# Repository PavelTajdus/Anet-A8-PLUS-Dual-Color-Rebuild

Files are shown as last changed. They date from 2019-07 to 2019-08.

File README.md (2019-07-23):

# Anet A8 PLUS Dual Color Rebuild

Kamarád chtěl postavit dual color tiskárnu. Jako základ pro dvoubarevný tisk jsem zvolil Anet A8Plus, která vypadala jako solidní základ pro předělávku. Později se ukázalo, že to nebyla nejšťastnější volba, ale tiskárna už byla doma, takže jsem si s tím musel poradit.

Protože tiskárna z výroby není moc dobře udělaná (profily nemají stejné délky - lítá to až o milimetr), závitovky nejsou rovné atd atd, musel jsem trochu přepracovat některé díly. Nakonec jsem toho přepracovával hodně :-)

Z původní tiskárny jsem použil profily, tyče, závitovky, motory, endstopy a pár kabelů. Zbytek jsem předělal.

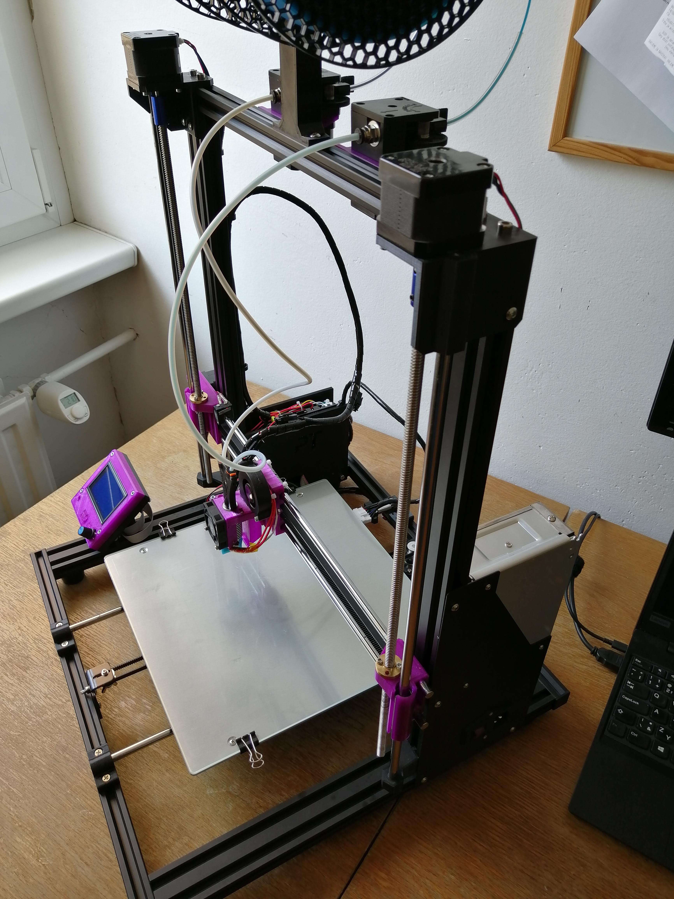
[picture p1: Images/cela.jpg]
PT Anet A8Plus Dual Color


## Dual Color

Jako systém pro dvoubarevný tisk jsem zvolil systém dvou extruderů do jednoho hotendu (Y joiner). Jedná se o relativně jednoduché řešení, které podporuje i mnou používaný Prusa Slicer 2.0.

Použil jsem klona V6 hotendu s bore 4.1 heatbreakem. Používá se proto, aby do hotendu šla tenčí PTFE o průměru 1,9mm, a do "joineru" pak klasická PTFE o průměru 2,0mm. Zabezpečí se tím hladší chod filamentu v "joineru".

## Vyměněné díly

Kvůli použití dvou extruderů jsem musel měnit i desku. Zvolil jsem SKR v1.3, což je 32bitová deska za výbornou cenu. Dokonce levnější než originální Anet deska. Origo deska má integrované drivery, takže jsem k SKR nakoupil 5x TMC2208, které jsem zapojil v UART. Díky tomu se dají drivery ovládat z Firmware a nastavovat jejich mod, hybrid treshold a jiné srandy.

Abych zajistil dostatečně kvalitní podávání filamentu, rozhodl jsem se pro Titan extruder (opět klony). Mám s nimi dobré zkušenosti - dobře se zavádí a vyndavá filament (oproti BMG). A je za super cenu.

Protože jsem nebyl absolutně schopný vyrovnat podložku standardními levlovacími šrouby, rozhodl jsem se pro 3Dtouch. Měl jsem dva různé senzory, jeden od Trianglelab, druhý od Fysetc. Fysetc skončil v koši. Absolutně k ničemu. Trianglelab naštěsti funguje obstojně. Podložku jsem přišrouboval napevno pomocí distančních sloupků.

Další výměna mě čekala u displeje. Nebyl jsem schopný rozhýbat originální přibalený displej, tak jsem použil klasický velký 12864 LCD displej se čtečkou karet. Čtečka karet v displeji je mnohem příjemnější pro obsluhu než lovit malou mikro sd kartu za tiskárnou v desce.

Měnil jsem i část kabeláže, protože například kabel od zdroje mi nedosáhl k desce, aniž by visel pod bedem. Kabeláž k hotendu jsem doplnil o konektory, aby se hotend dal kompletně sundat bez nutnosti odpojování kabeláže z desky. Veškerou kabeláž jsem pak omotal omotávkou dodávanou k tiskárně a kabely přichytil do profilů spojkami.

### Motory vzhůru!

Umístit motory nahoře bylo řešením několika problémů. Závitové tyče nebyly naprosto rovné. Jedna ano, druhá ne. Při otáčení závitovkou tyč ovlivňovala osu X, což ovlivní kvalitu tisku. Další problém byl, že došlo ke snížení bedu o nějaký ten centimetr a díky změně hotendu a extruderu už nebylo možné dostat se tryskou na tiskovou podložku. Umístěním motorů nahoru všechny tyhle neduhy vyřešilo. A nepřišlo se ani o milimetr z tiskové výšky stroje. Naopak by se dalo ještě pár cm přidat, ale na úkor snížení pevnosti držáků motoru. Což mi přišlo zbytečné.

## Seznam dokoupených dílů

### Elektronika
- [Deska SKR V1.3](https://www.aliexpress.com/item/32980090169.html)
- [5x TMC 2208](https://www.aliexpress.com/item/32980090169)
- [Motor extruderu](https://www.aliexpress.com/item/32377416566.html)
- [Dlouhé kabely k motorům](https://www.aliexpress.com/item/33015610522.html)
- [Rozdvojka konektorů pro Z motory](https://www.aliexpress.com/item/32849801852.html)
- [Trianglelab 3D Touch](https://www.aliexpress.com/item/32832887426.html)
- [12864 LCD displej se čtečkou karet](https://www.aliexpress.com/item/32516184695.html)
- [Stepdowny na 12V](https://www.aliexpress.com/item/32725444495.html)
- [5015 ventilátor Sunon 12V - ofuk výtisku](https://www.official.cz/z5376-ventilator-sunon-gb1205phvx-8ay-gn)
- [4010 ventilátor Sunon 12V - hotend](https://www.gme.cz/ventilator-sunon-ee40101s2-1000u-999)
- [6015 ventilátor Sunon 12V - do zdroje](https://www.gme.cz/ventilator-sunon-kd1206phs3)
- [50x50 tichý ventilátor Sillentium PC 12V - ofuk desky](https://www.czc.cz/silentiumpc-zephyr-50-50mm/134487/produkt)
- [Přívodní kabely průměr 4mm ze zdroje k desce](https://www.emat.cz/index.php?route=product/search&search=H07V-K%204)
- [Konektory pro připojení endstopů a další kabeláže do desky (XH2.54 2 Pin)](https://www.aliexpress.com/item/32821493939.html)
- [Konektory pro spojení kabeláže hotendu](https://www.aliexpress.com/item/32843315324.html)

### Hardware
- [Titan Extruder](https://www.aliexpress.com/item/32789942768.html)
- [V6 hotend 4.1 bore](https://www.aliexpress.com/item/32911028903.html)
- [Silikonový návlek na hotend](https://www.aliexpress.com/item/32920518452.html)
- [Trianglelab TL-Feeder ("joiner" - Y spojka)](https://www.aliexpress.com/item/32770576556.html)
- [PTFE (ačkoliv jsou dodané k joineru, dával jsem jiné)](https://www.aliexpress.com/item/32814232529.html)
- [Distanční sloupky k bedu](https://www.gme.cz/distancni-trubicka-mdr4305)
- [Pevné spojky závitové tyče a motoru 5x8mm](https://www.aliexpress.com/item/32957956109.html)
- [Ložisko LM8UU (vozík osy x)](https://www.aliexpress.com/item/32317938156.html)
- [Šrouby M4 různých délek](https://eshop.killich.cz/eshop/nerezovy-spojovaci-material/srouby-zatky/imbusy-vnitrni-sestihran/din-912-imbus-s-valcovou-hlavou/)
- [Stahovací pásky](https://www.aliexpress.com/item/32868074097.html)
- [Matky do profilů M4](https://www.aliexpress.com/item/32799858611.html)

### Tištěné díly

Viz seznam dílů [ve složce STL](https://github.com/PavelTajdus/Anet-A8-PLUS-Dual-Color-Rebuild/tree/master/STL).

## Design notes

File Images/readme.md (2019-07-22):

PT Anet A8Plus Dual Color
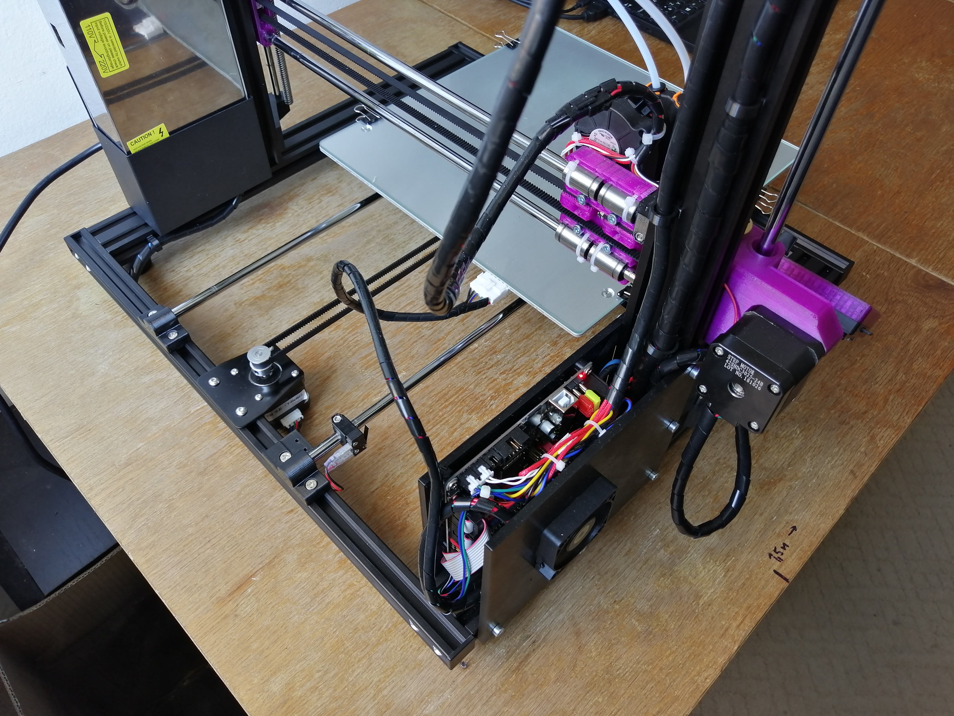
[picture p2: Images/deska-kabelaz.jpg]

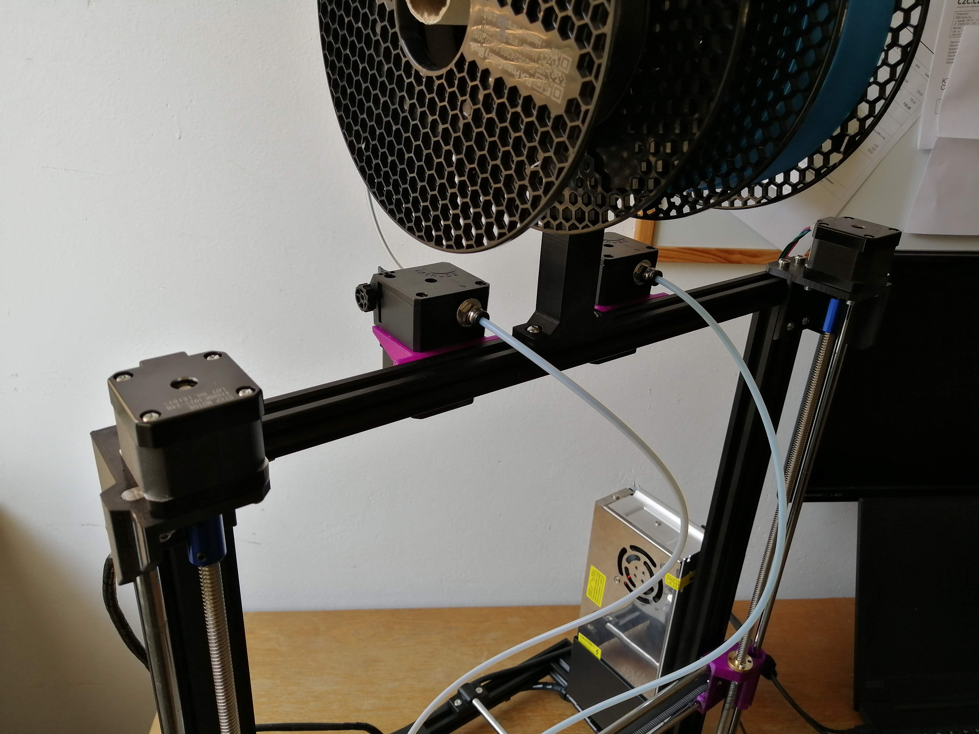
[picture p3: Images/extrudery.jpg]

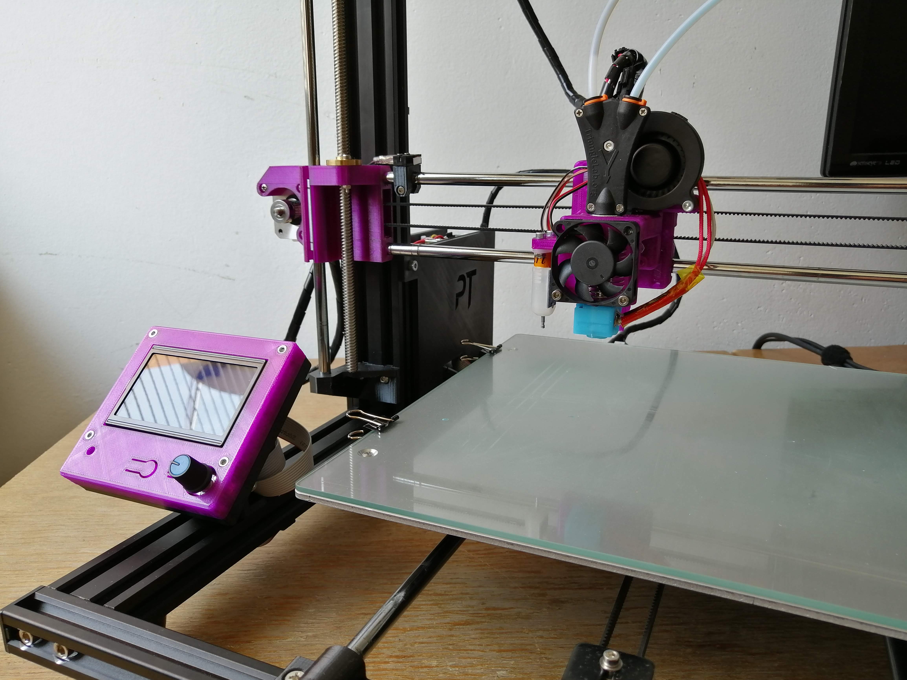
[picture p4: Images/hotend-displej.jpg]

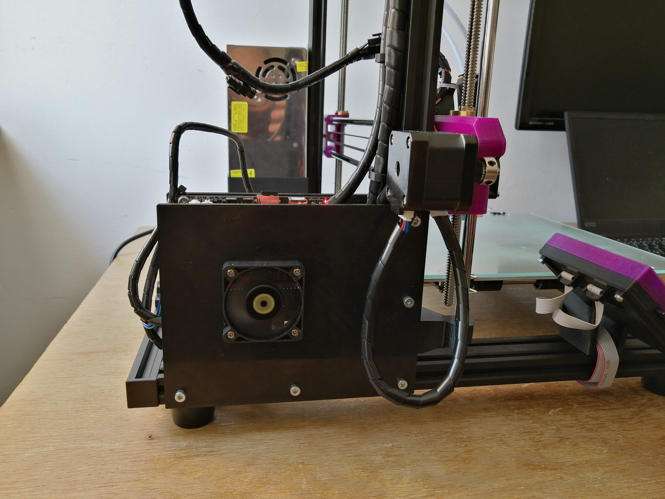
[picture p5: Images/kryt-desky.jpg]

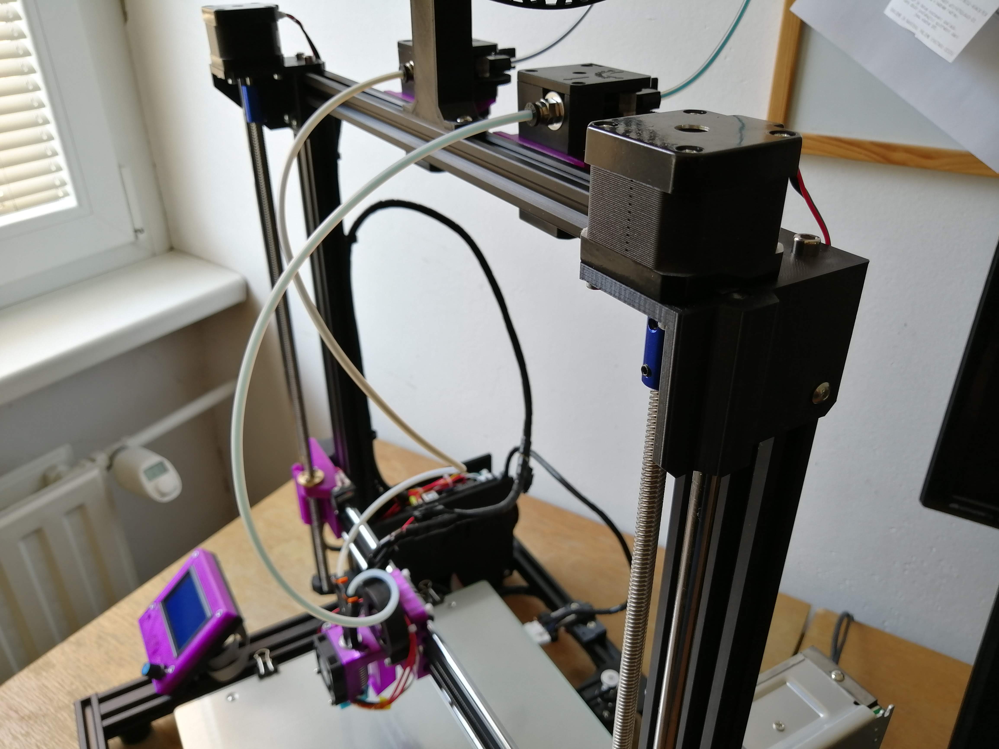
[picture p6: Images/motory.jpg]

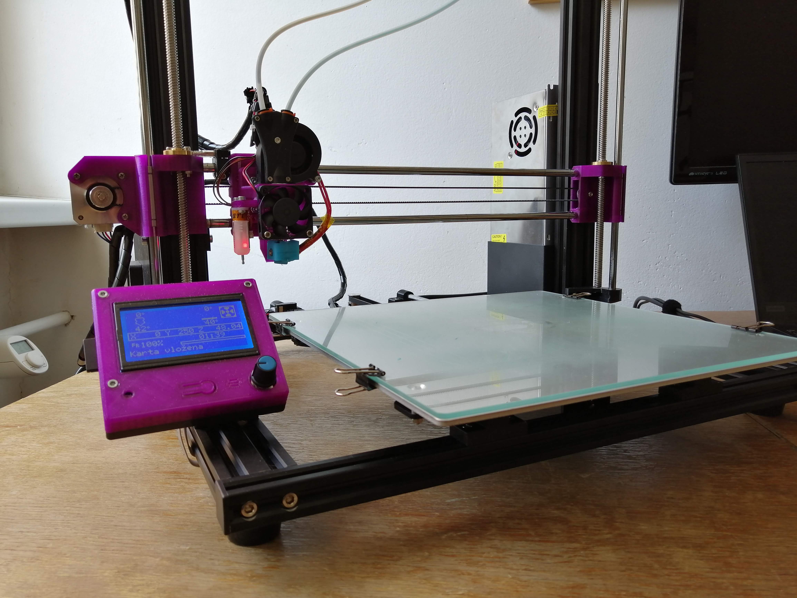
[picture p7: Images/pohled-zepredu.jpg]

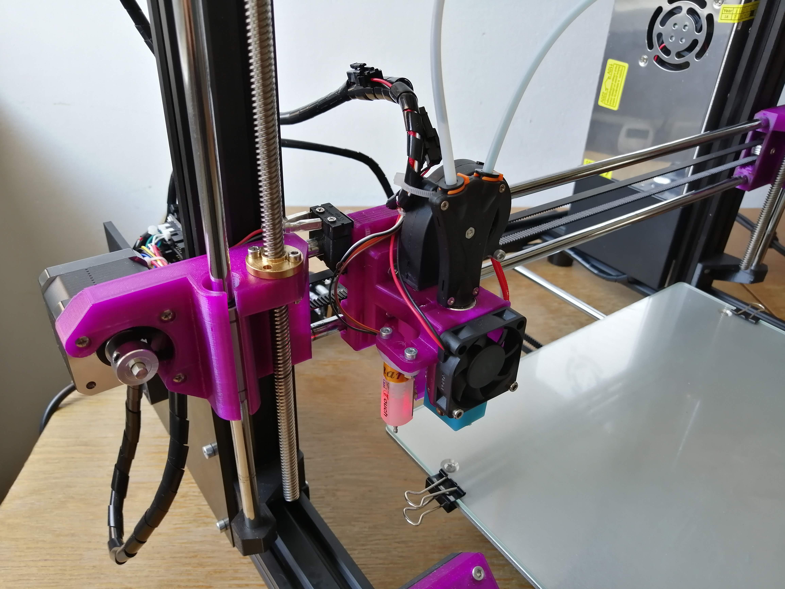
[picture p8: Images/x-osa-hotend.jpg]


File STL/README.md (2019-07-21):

# STL soubory pro přestavbu tiskárny

Většinu dílů jsem si navrhl, protože jsem nebyl schopný najít odpovídající řešení na thingiverse nebo jinde. Díly které jsem nenavrhoval zde uvádím v odkaze na thingiverse. Ale zároveň je najdete zde jako STL.

Kompletně jsem předělal osu X. Anet používá jiné rozměry než i3 standard, což mě omezovalo v použítí různých pojezdů a držáků hotendu. Proto jsem předělal osu X aby používala rozteč tyčí 45 mm.

Kvůli zvolenému systému pro Dual Color jsem vybral V6 hotend s bore 4.1 heatbreakem. A použil oblíbený držák z Hypercube. Používám 40mm větráky, a 3Dtouch. Veškeré díly jsou jak v STL souborech, tak v odkazech.

## Odkazy na použité komponenty:
- [Kryt na displej - Discount Full Graphic Smart Controller](https://www.thingiverse.com/thing:2368534)
- [Držák V6 hotendu](https://www.thingiverse.com/thing:1632847)
- [Redukce na 40mm ventilátor pro držák hotendu](https://www.thingiverse.com/thing:2716350)
- [X vozík pro hotend](https://www.thingiverse.com/thing:586636)

### Doporučené příslušenství

- [Klipy na kabely](https://www.thingiverse.com/thing:3102684)
- [Klipy na kabely k displeji](https://www.thingiverse.com/thing:2626246)

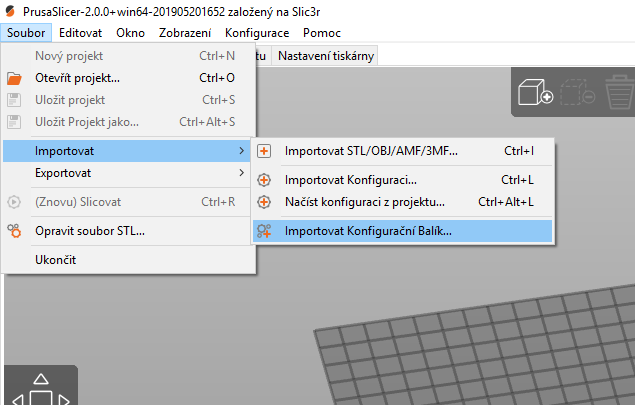
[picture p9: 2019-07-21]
Images/import-balicku.png

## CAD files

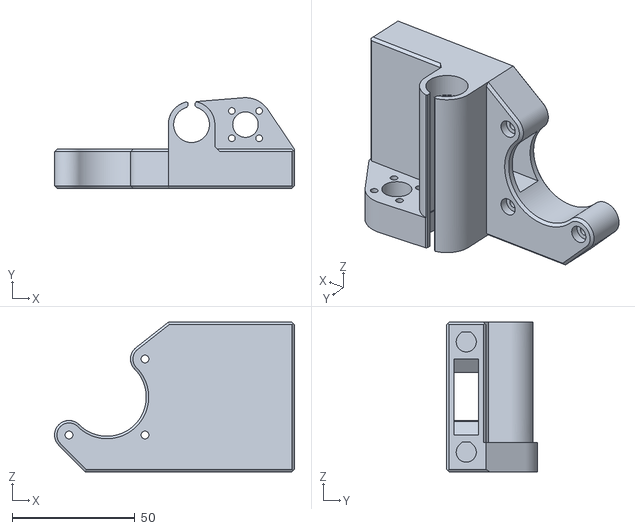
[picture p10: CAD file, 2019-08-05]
STL/x-osa-motor-idler.stl
97.9 x 37.0 x 61.0

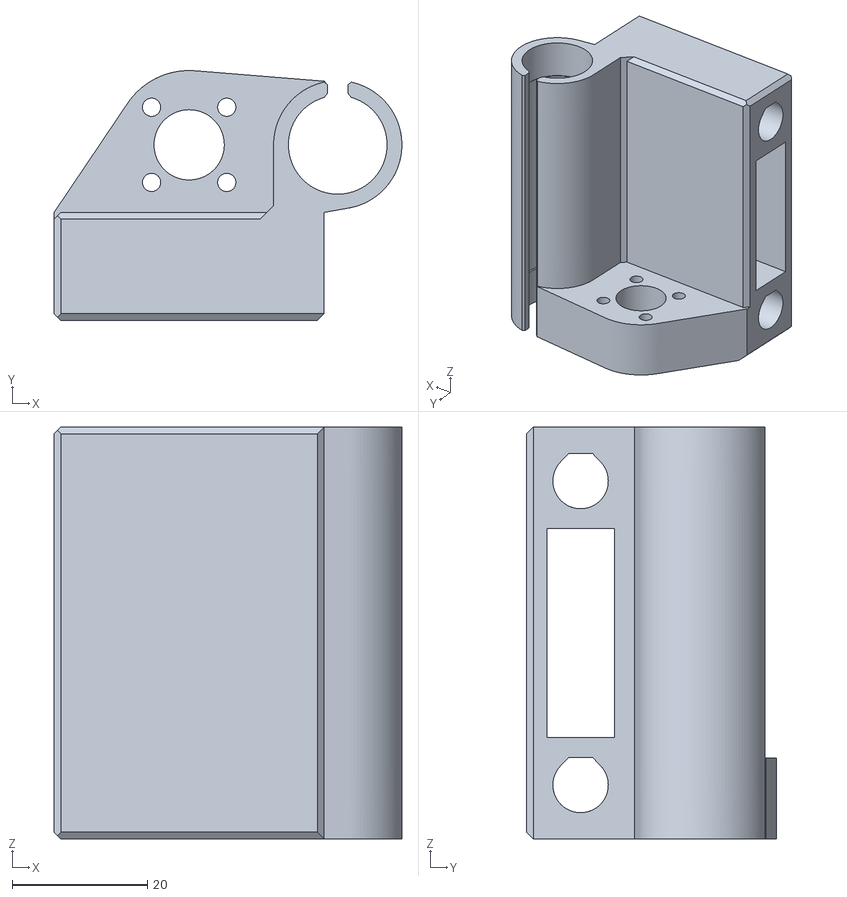
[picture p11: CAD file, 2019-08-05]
STL/x-osa-idler.stl
51.5 x 37.0 x 61.0

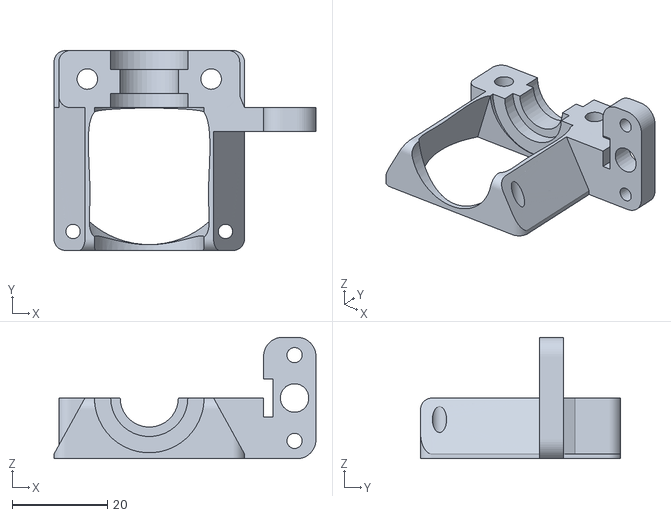
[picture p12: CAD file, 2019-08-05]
STL/redukce-40mm-vetrak-na-hotend.stl
55.0 x 42.0 x 25.5

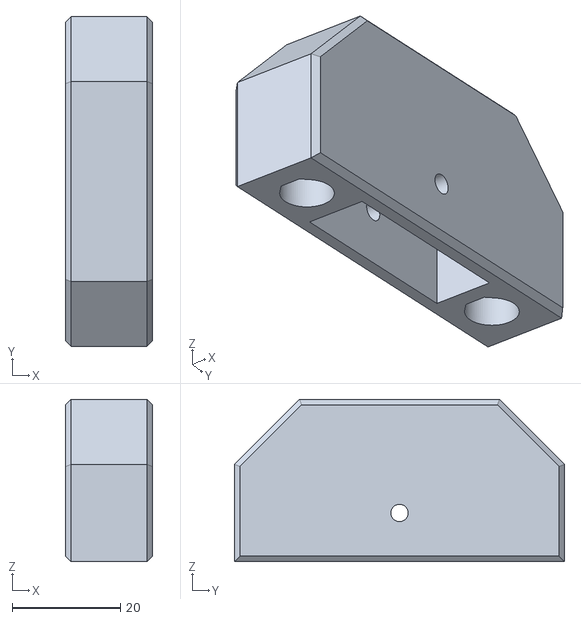
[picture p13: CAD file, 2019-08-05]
STL/x-drzak-remene.stl
16.0 x 61.0 x 30.0

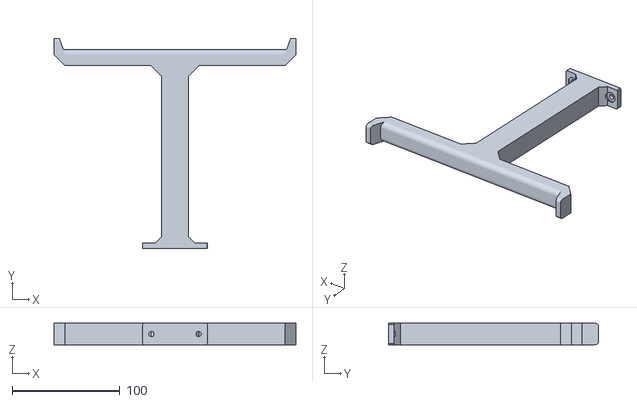
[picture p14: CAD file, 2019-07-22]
STL/dualni-drzak-filamentu.stl
225.0 x 195.3 x 20.0

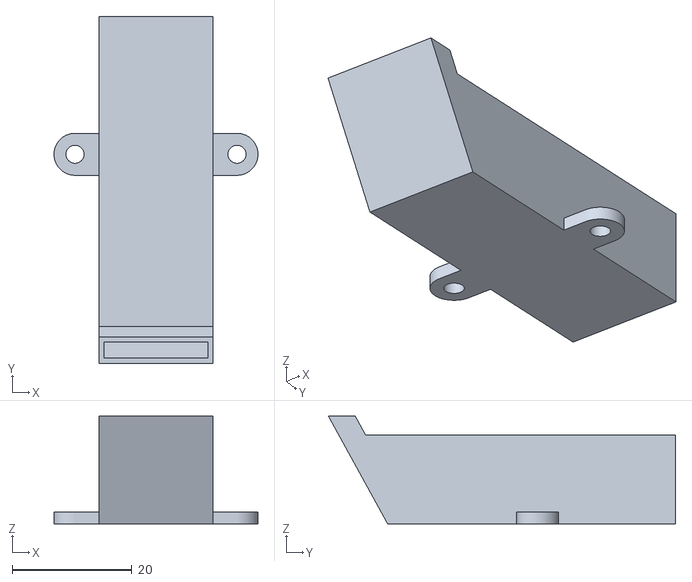
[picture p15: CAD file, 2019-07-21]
STL/ofuk-tisku.stl
34.0 x 57.9 x 18.0

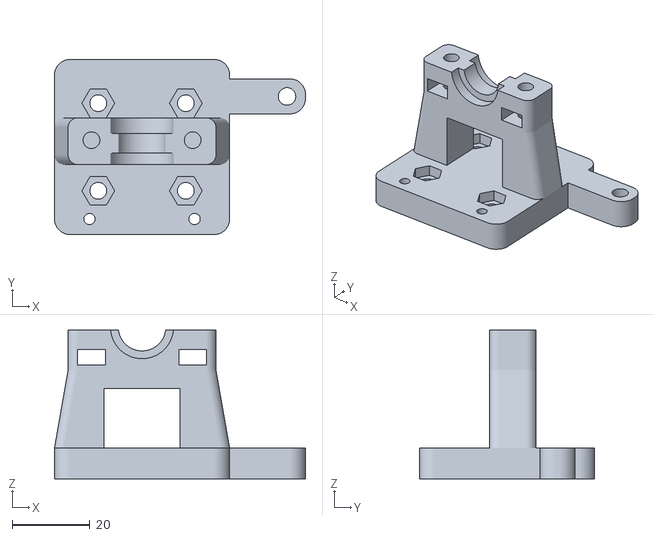
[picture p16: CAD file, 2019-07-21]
STL/drzak-hotendu.stl
64.5 x 45.0 x 38.2

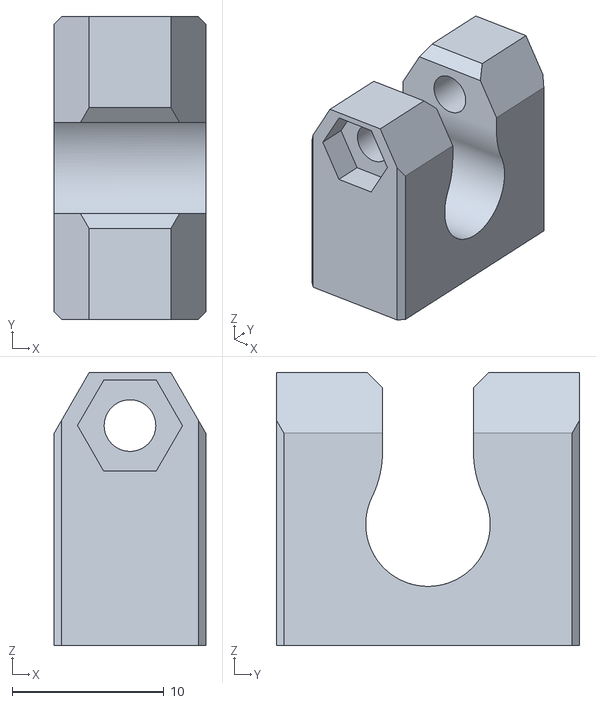
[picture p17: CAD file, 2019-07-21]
STL/drzak-koncoveho-spinace-x-y.stl
10.0 x 20.0 x 18.0

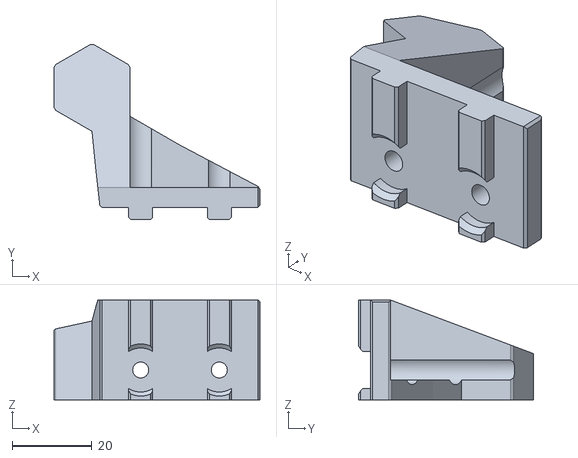
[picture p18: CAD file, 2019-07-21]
STL/drzak-tyce-levy.stl
51.5 x 43.7 x 25.0

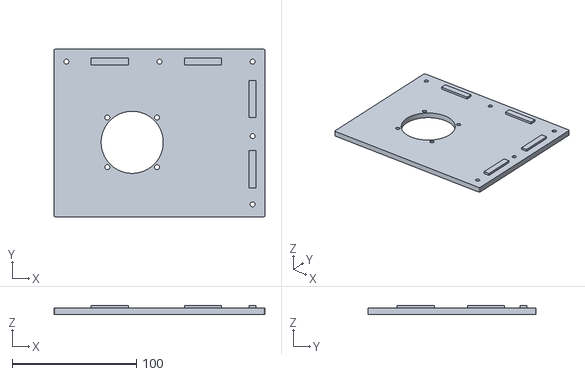
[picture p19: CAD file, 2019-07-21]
STL/kryt-SKR-desky.stl
170.0 x 135.0 x 7.00

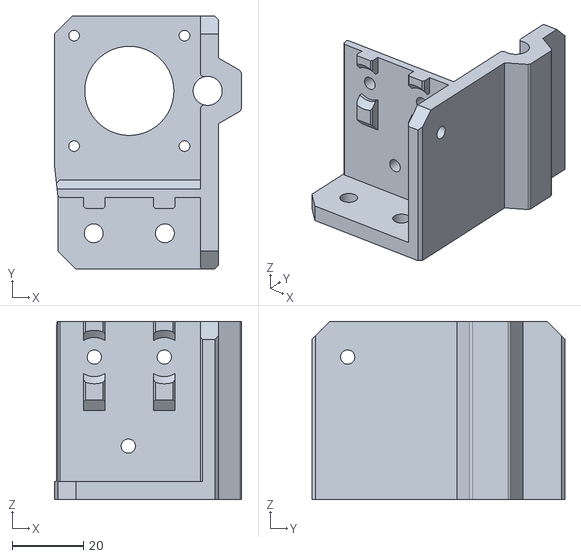
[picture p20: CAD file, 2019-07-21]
STL/drzak-motoru-pravy.stl
52.5 x 71.0 x 50.0

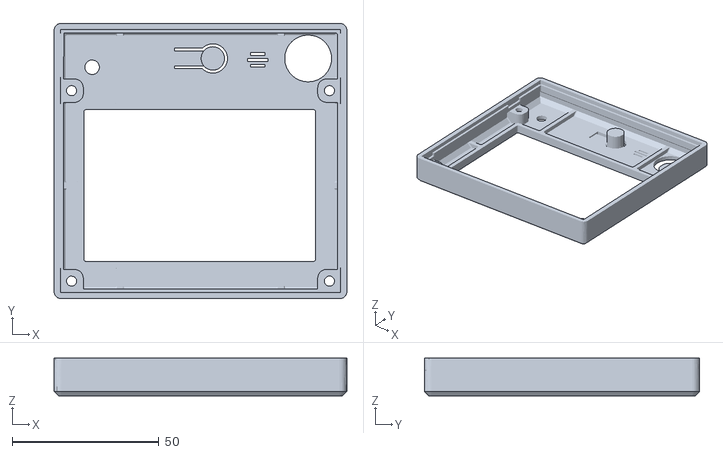
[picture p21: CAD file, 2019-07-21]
STL/horni-kryt-displeje.stl
100.0 x 94.0 x 12.8

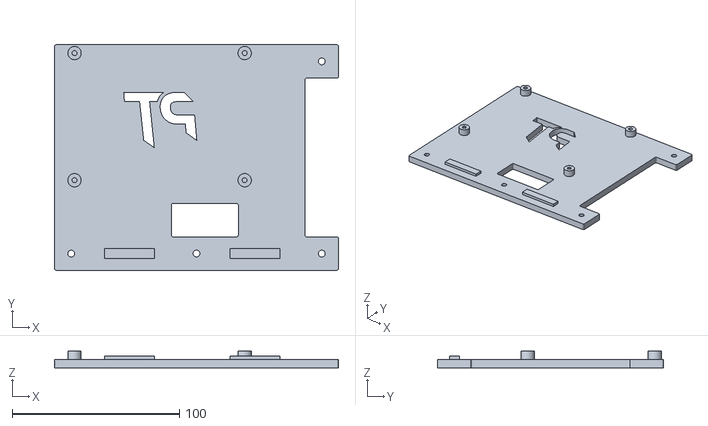
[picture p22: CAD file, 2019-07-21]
STL/drzak-SKR-desky.stl
170.0 x 135.0 x 10.00

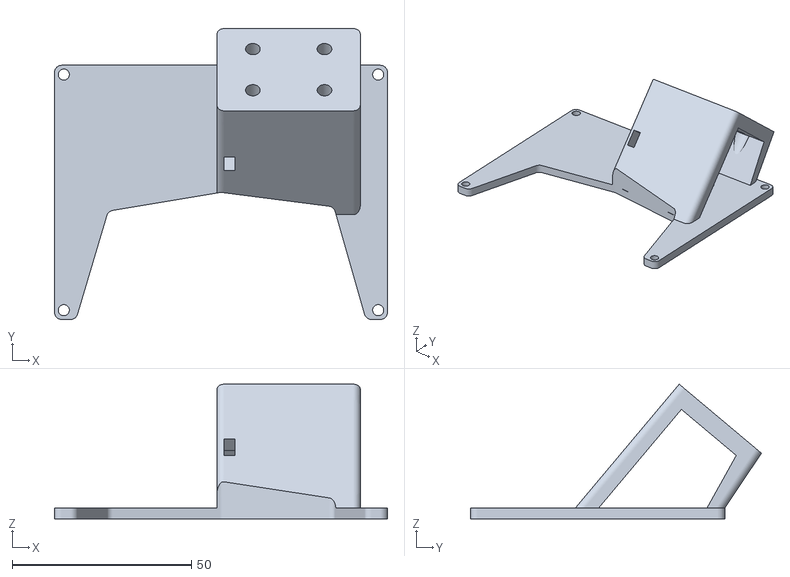
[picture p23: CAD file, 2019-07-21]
STL/drzak-displeje.stl
93.0 x 81.3 x 37.6

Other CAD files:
STL/drzak-tyce-pravy.stl
STL/drzak-motoru-levy.stl
STL/x-pojezd-pro-hotend.stl

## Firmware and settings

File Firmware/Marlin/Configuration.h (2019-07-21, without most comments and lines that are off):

#pragma once
#define CONFIGURATION_H_VERSION 020000
#define STRING_CONFIG_H_AUTHOR "(Pavel Tajdus, Anet A8P SKR config)" // Who made the changes.
#define STRING_SPLASH_LINE1 SHORT_BUILD_VERSION // will be shown during bootup in line 1
#define STRING_SPLASH_LINE2 WEBSITE_URL         // will be shown during bootup in line 2
#define SERIAL_PORT -1
#define SERIAL_PORT_2 0
#define BAUDRATE 250000
  #define MOTHERBOARD BOARD_BIGTREE_SKR_V1_3
#define CUSTOM_MACHINE_NAME "PT-DUAL MK1"
#define EXTRUDERS 2
#define DEFAULT_NOMINAL_FILAMENT_DIA 1.75
#define SINGLENOZZLE
#define TEMP_SENSOR_0 1
#define TEMP_SENSOR_1 0
#define TEMP_SENSOR_2 0
#define TEMP_SENSOR_3 0
#define TEMP_SENSOR_4 0
#define TEMP_SENSOR_5 0
#define TEMP_SENSOR_BED 1
#define TEMP_SENSOR_CHAMBER 0
#define DUMMY_THERMISTOR_998_VALUE 25
#define DUMMY_THERMISTOR_999_VALUE 100
#define MAX_REDUNDANT_TEMP_SENSOR_DIFF 10
#define TEMP_RESIDENCY_TIME     10  // (seconds) Time to wait for hotend to "settle" in M109
#define TEMP_WINDOW              1  // (°C) Temperature proximity for the "temperature reached" timer
#define TEMP_HYSTERESIS          3  // (°C) Temperature proximity considered "close enough" to the target
#define TEMP_BED_RESIDENCY_TIME 10  // (seconds) Time to wait for bed to "settle" in M190
#define TEMP_BED_WINDOW          1  // (°C) Temperature proximity for the "temperature reached" timer
#define TEMP_BED_HYSTERESIS      3  // (°C) Temperature proximity considered "close enough" to the target
#define HEATER_0_MINTEMP   5
#define HEATER_1_MINTEMP   5
#define HEATER_2_MINTEMP   5
#define HEATER_3_MINTEMP   5
#define HEATER_4_MINTEMP   5
#define HEATER_5_MINTEMP   5
#define BED_MINTEMP        5
#define HEATER_0_MAXTEMP 260
#define HEATER_1_MAXTEMP 260
#define HEATER_2_MAXTEMP 260
#define HEATER_3_MAXTEMP 260
#define HEATER_4_MAXTEMP 260
#define HEATER_5_MAXTEMP 260
#define BED_MAXTEMP      125
#define PIDTEMP
#define BANG_MAX 255     // Limits current to nozzle while in bang-bang mode; 255=full current
#define PID_MAX BANG_MAX // Limits current to nozzle while PID is active (see PID_FUNCTIONAL_RANGE below); 255=full current
#define PID_K1 0.95      // Smoothing factor within any PID loop
  #define PID_FUNCTIONAL_RANGE 10 // If the temperature difference between the target temperature and the actual temperature
  #define DEFAULT_Kp 16.87
  #define DEFAULT_Ki 1.29
  #define DEFAULT_Kd 55.04
#define MAX_BED_POWER 255 // limits duty cycle to bed; 255=full current
#define PREVENT_COLD_EXTRUSION
#define EXTRUDE_MINTEMP 170
#define PREVENT_LENGTHY_EXTRUDE
#define EXTRUDE_MAXLENGTH 200
#define THERMAL_PROTECTION_HOTENDS // Enable thermal protection for all extruders
#define THERMAL_PROTECTION_BED     // Enable thermal protection for the heated bed
#define THERMAL_PROTECTION_CHAMBER // Enable thermal protection for the heated chamber
#define USE_XMIN_PLUG
#define USE_YMIN_PLUG
#define USE_ZMIN_PLUG
#define ENDSTOPPULLUPS
#define X_MIN_ENDSTOP_INVERTING true // set to true to invert the logic of the endstop.
#define Y_MIN_ENDSTOP_INVERTING true // set to true to invert the logic of the endstop.
#define Z_MIN_ENDSTOP_INVERTING true // set to true to invert the logic of the endstop.
#define X_MAX_ENDSTOP_INVERTING false // set to true to invert the logic of the endstop.
#define Y_MAX_ENDSTOP_INVERTING false // set to true to invert the logic of the endstop.
#define Z_MAX_ENDSTOP_INVERTING false // set to true to invert the logic of the endstop.
#define Z_MIN_PROBE_ENDSTOP_INVERTING true // set to true to invert the logic of the probe.
#define X_DRIVER_TYPE  TMC2208
#define Y_DRIVER_TYPE  TMC2208
#define Z_DRIVER_TYPE  TMC2208
#define E0_DRIVER_TYPE TMC2208
#define E1_DRIVER_TYPE TMC2208
#define DISTINCT_E_FACTORS
#define DEFAULT_AXIS_STEPS_PER_UNIT   { 80, 80, 400, 395, 395 }
#define DEFAULT_MAX_FEEDRATE          { 300, 300, 50, 50, 50 }
#define DEFAULT_MAX_ACCELERATION      { 1500, 1500, 100, 5000 }
#define DEFAULT_ACCELERATION          1000    // X, Y, Z and E acceleration for printing moves
#define DEFAULT_RETRACT_ACCELERATION  1000    // E acceleration for retracts
#define DEFAULT_TRAVEL_ACCELERATION   1000    // X, Y, Z acceleration for travel (non printing) moves
  #define DEFAULT_XJERK 10.0
  #define DEFAULT_YJERK 10.0
  #define DEFAULT_ZJERK  0.3
#define DEFAULT_EJERK    5.0  // May be used by Linear Advance
#define S_CURVE_ACCELERATION
#define Z_MIN_PROBE_USES_Z_MIN_ENDSTOP_PIN
#define BLTOUCH
#define X_PROBE_OFFSET_FROM_EXTRUDER -35 // X offset: -left  +right  [of the nozzle]
#define Y_PROBE_OFFSET_FROM_EXTRUDER 0  // Y offset: -front +behind [the nozzle]
#define Z_PROBE_OFFSET_FROM_EXTRUDER -1   // Z offset: -below +above  [the nozzle]
#define MIN_PROBE_EDGE 60
#define XY_PROBE_SPEED (40*60)
#define Z_PROBE_SPEED_FAST HOMING_FEEDRATE_Z
#define Z_PROBE_SPEED_SLOW (Z_PROBE_SPEED_FAST / 2)
#define MULTIPLE_PROBING 3
#define Z_CLEARANCE_DEPLOY_PROBE   10 // Z Clearance for Deploy/Stow
#define Z_CLEARANCE_BETWEEN_PROBES  6 // Z Clearance between probe points
#define Z_CLEARANCE_MULTI_PROBE     4 // Z Clearance between multiple probes
#define Z_AFTER_PROBING            10 // Z position after probing is done
#define Z_PROBE_LOW_POINT          -2 // Farthest distance below the trigger-point to go before stopping
#define Z_PROBE_OFFSET_RANGE_MIN -20
#define Z_PROBE_OFFSET_RANGE_MAX 20
#define Z_MIN_PROBE_REPEATABILITY_TEST
#define X_ENABLE_ON 0
#define Y_ENABLE_ON 0
#define Z_ENABLE_ON 0
#define E_ENABLE_ON 0 // For all extruders
#define DISABLE_X false
#define DISABLE_Y false
#define DISABLE_Z false
#define DISABLE_E false             // For all extruders
#define DISABLE_INACTIVE_EXTRUDER   // Keep only the active extruder enabled
#define INVERT_X_DIR true
#define INVERT_Y_DIR false
#define INVERT_Z_DIR true
#define INVERT_E0_DIR true
#define INVERT_E1_DIR true
#define INVERT_E2_DIR false
#define INVERT_E3_DIR false
#define INVERT_E4_DIR false
#define INVERT_E5_DIR false
#define Z_HOMING_HEIGHT 10  // (mm) Minimal Z height before homing (G28) for Z clearance above the bed, clamps, ...
#define X_HOME_DIR -1
#define Y_HOME_DIR -1
#define Z_HOME_DIR -1
#define X_BED_SIZE 300
#define Y_BED_SIZE 300
#define X_MIN_POS 0
#define Y_MIN_POS 0
#define Z_MIN_POS 0
#define X_MAX_POS X_BED_SIZE
#define Y_MAX_POS Y_BED_SIZE
#define Z_MAX_POS 350
#define MIN_SOFTWARE_ENDSTOPS
  #define MIN_SOFTWARE_ENDSTOP_X
  #define MIN_SOFTWARE_ENDSTOP_Y
  #define MIN_SOFTWARE_ENDSTOP_Z
#define MAX_SOFTWARE_ENDSTOPS
  #define MAX_SOFTWARE_ENDSTOP_X
  #define MAX_SOFTWARE_ENDSTOP_Y
  #define MAX_SOFTWARE_ENDSTOP_Z
#define AUTO_BED_LEVELING_BILINEAR
  #define ENABLE_LEVELING_FADE_HEIGHT
  #define SEGMENT_LEVELED_MOVES
  #define LEVELED_SEGMENT_LENGTH 5.0 // (mm) Length of all segments (except the last one)
  #define GRID_MAX_POINTS_X 3
  #define GRID_MAX_POINTS_Y GRID_MAX_POINTS_X
#define LCD_BED_LEVELING
  #define MESH_EDIT_Z_STEP  0.025 // (mm) Step size while manually probing Z axis.
  #define LCD_PROBE_Z_RANGE 4     // (mm) Z Range centered on Z_MIN_POS for LCD Z adjustment
#define Z_SAFE_HOMING
  #define Z_SAFE_HOMING_X_POINT ((X_BED_SIZE) / 2)    // X point for Z homing when homing all axes (G28).
  #define Z_SAFE_HOMING_Y_POINT ((Y_BED_SIZE) / 2)    // Y point for Z homing when homing all axes (G28).
#define HOMING_FEEDRATE_XY (40*60)
#define HOMING_FEEDRATE_Z  (4*60)
#define VALIDATE_HOMING_ENDSTOPS
#define EEPROM_SETTINGS     // Persistent storage with M500 and M501
#define EEPROM_CHITCHAT       // Give feedback on EEPROM commands. Disable to save PROGMEM.
#define HOST_KEEPALIVE_FEATURE        // Disable this if your host doesn't like keepalive messages
#define DEFAULT_KEEPALIVE_INTERVAL 2  // Number of seconds between "busy" messages. Set with M113.
#define BUSY_WHILE_HEATING            // Some hosts require "busy" messages even during heating
#define PREHEAT_1_LABEL       "PLA"
#define PREHEAT_1_TEMP_HOTEND 210
#define PREHEAT_1_TEMP_BED     60
#define PREHEAT_1_FAN_SPEED     0 // Value from 0 to 255
#define PREHEAT_2_LABEL       "PETG"
#define PREHEAT_2_TEMP_HOTEND 235
#define PREHEAT_2_TEMP_BED     60
#define PREHEAT_2_FAN_SPEED     0 // Value from 0 to 255
#define NOZZLE_PARK_FEATURE
  #define NOZZLE_PARK_POINT { (X_MIN_POS + 10), (Y_MAX_POS - 10), 20 }
  #define NOZZLE_PARK_XY_FEEDRATE 100   // (mm/s) X and Y axes feedrate (also used for delta Z axis)
  #define NOZZLE_PARK_Z_FEEDRATE 5      // (mm/s) Z axis feedrate (not used for delta printers)
#define PRINTJOB_TIMER_AUTOSTART
#define LCD_LANGUAGE cz
#define DISPLAY_CHARSET_HD44780 WESTERN
#define LCD_INFO_SCREEN_STYLE 0
#define SDSUPPORT
#define SD_CHECK_AND_RETRY
#define REVERSE_ENCODER_DIRECTION
#define SPEAKER
#define REPRAP_DISCOUNT_FULL_GRAPHIC_SMART_CONTROLLER
#define SOFT_PWM_SCALE 0
#define SERVO_DELAY { 300 }

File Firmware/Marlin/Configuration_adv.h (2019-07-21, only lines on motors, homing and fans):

#define E0_AUTO_FAN_PIN FAN1_PIN
#define E1_AUTO_FAN_PIN -1
#define E2_AUTO_FAN_PIN -1
#define E3_AUTO_FAN_PIN -1
#define E4_AUTO_FAN_PIN -1
#define E5_AUTO_FAN_PIN -1
#define CHAMBER_AUTO_FAN_PIN -1
#define X_HOME_BUMP_MM 4
#define Y_HOME_BUMP_MM 3
#define Z_HOME_BUMP_MM 3
#define HOMING_BUMP_DIVISOR { 2, 2, 4 }  // Re-Bump Speed Divisor (Divides the Homing Feedrate)
#define QUICK_HOME                     // If homing includes X and Y, do a diagonal move initially
#define MICROSTEP_MODES { 16, 16, 16, 16, 16, 16 } // [1,2,4,8,16]
#define DIGIPOT_I2C_MOTOR_CURRENTS { 1.0, 1.0, 1.0, 1.0, 1.0, 1.0, 1.0, 1.0 }  //  AZTEEG_X3_PRO
#define ADVANCED_PAUSE_FEATURE
  #define ADVANCED_PAUSE_PURGE_FEEDRATE        3  // (mm/s) Extrude feedrate (after loading). Should be slower than load feedrate.
  #define ADVANCED_PAUSE_PURGE_LENGTH         50  // (mm) Length to extrude after loading.
  #define ADVANCED_PAUSE_RESUME_PRIME          0  // (mm) Extra distance to prime nozzle after returning from park.
    #define X_CURRENT     550  // (mA) RMS current. Multiply by 1.414 for peak current.
    #define X_MICROSTEPS   16  // 0..256
    #define Y_CURRENT     550
    #define Y_MICROSTEPS   16
    #define Z_CURRENT     700
    #define Z_MICROSTEPS   16
    #define E0_CURRENT    550
    #define E0_MICROSTEPS  16
    #define E1_CURRENT    550
    #define E1_MICROSTEPS  16
    #define CURRENT_STEP_DOWN     50  // [mA]
    #define REPORT_CURRENT_CHANGE
  #define HYBRID_THRESHOLD
  #define X_HYBRID_THRESHOLD     100  // [mm/s]
  #define X2_HYBRID_THRESHOLD    100
  #define Y_HYBRID_THRESHOLD     100
  #define Y2_HYBRID_THRESHOLD    100
  #define Z_HYBRID_THRESHOLD       3
  #define Z2_HYBRID_THRESHOLD      3
  #define Z3_HYBRID_THRESHOLD      3
  #define E0_HYBRID_THRESHOLD     40
  #define E1_HYBRID_THRESHOLD     40
  #define E2_HYBRID_THRESHOLD     40
  #define E3_HYBRID_THRESHOLD     40
  #define E4_HYBRID_THRESHOLD     40
  #define E5_HYBRID_THRESHOLD     40

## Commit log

2019-07-21 První commit
    [Configuration.h, Configuration_adv.h, drzak-SKR-desky.stl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]
2019-07-22 Doplnění držáku a popisu
    [dualni-drzak-filamentu.stl]
2019-07-23 Doplněné info o motorech
2019-08-05 Úprava osy X
    Doplněn držák řemene pro pojezd osy X. Pravý idler (vozík) již není ovlivňován napnutím řemene, a celou sílu řemene teď drží tyče osy x.
    [redukce-40mm-vetrak-na-hotend.stl, x-drzak-remene.stl, x-osa-idler.stl]
2019-08-05 Dizajnové úpravy držáku motoru.
    [x-osa-motor-idler.stl]

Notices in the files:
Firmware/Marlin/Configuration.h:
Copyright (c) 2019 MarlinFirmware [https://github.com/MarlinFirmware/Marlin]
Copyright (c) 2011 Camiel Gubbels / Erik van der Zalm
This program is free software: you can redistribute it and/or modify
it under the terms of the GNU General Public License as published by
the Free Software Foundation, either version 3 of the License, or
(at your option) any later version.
